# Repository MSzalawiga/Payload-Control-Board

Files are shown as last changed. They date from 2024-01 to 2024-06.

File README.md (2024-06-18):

# Payload Control Board

During the 2023-2024 design cycle I was tasked with updating the Control Board for the Scientific Payload for Queen's Space Engineering Team.

I worked on 2 revisions of the board being Rev2 and Rev3 with Rev3 being the board used at competition.

These boards were created using KiCad 7.0 and were both 4 layer Signal/Ground/Power/Signal stackups.

## Revision 2
Revision 2 was done in a hurry as we needed a working control board for our systems acceptance review in late Feburary 2024, meaning I needed to order the board early December 2023 before exams started. The hurry comes from the fact that I took over this project from scratch in late November 2023.

### Scope and Functional Requirements
The scope and requirements of this control board came from the requirements from the Science and Mechanical team along with the 2024 University Rover Challenge (URC) Science mission rules. The scope and requirements were as follows:
- Control 2 Stepper Motors to raise and lower the payload
- Control up to 6 Servos for collection scoops and an auger
- Be able to toggle and change the brightness of 9 incandescent lights for the on-board spectrometer.
- Interface with the Rover through serial communication
- Interface with Sensors to get scientific measurements
### Reflection
I am content the turnout of this board, although the board was not space efficent it was able to serve its purpose in being able to provide funcionality for the systems acceptance review. 
Also since I was only able to use THT components (annoying I know) I couldn't find a buck converter with an external control pin, thankfully a weird trick I found online (can't find the articel :(  using a dac to influence the reading on the feedback pin worked wonderfully.

## Revision 3
Now having more time I created Revision 3, having mostly the same requirements with some exceptions being no more ethernet module, switch 3 lights for UV lights and the sensors switching it was pretty much the same. Also I could use SMT components (thank god). 

I am going to jump right into the reflection since the requirements were basically the same as revision 2.

### Reflection
Awesome, I am very happy with the turnout of this board. I was able to fit everything on a 100mm x 100mm board with a Teensy 4.1 microcontroller with a footprint of ~ 60mm x 25 mm. Also this was my first time soldering SMT components on a PCB so I chose 0603 (metric) to be my smallest passive size and I think it turned out well.

A new revision will be needed next year to adapt to the changing ruleset of the science mission. Next year I have taken on an executive position so I will be in more of a helper / design verification role for this specific project.

Some improvements I can think of are:
- No teensy 4.1, switch to STM32 they are just better and putting the MCU ourselves results in a smaller footprint and a more professional look
- I accidentally swapped SDA and SCL on the 3V3 I2C line (whoops) but with design verification next year this shouldn't happen
- For controlling light brightness use PWM and Transistors rather than a buck converter, the lights don't draw too much current. or use a newer buck ic with external pwm signal
- get new stepper drivers, current ones ran very hot and weren't very configurable

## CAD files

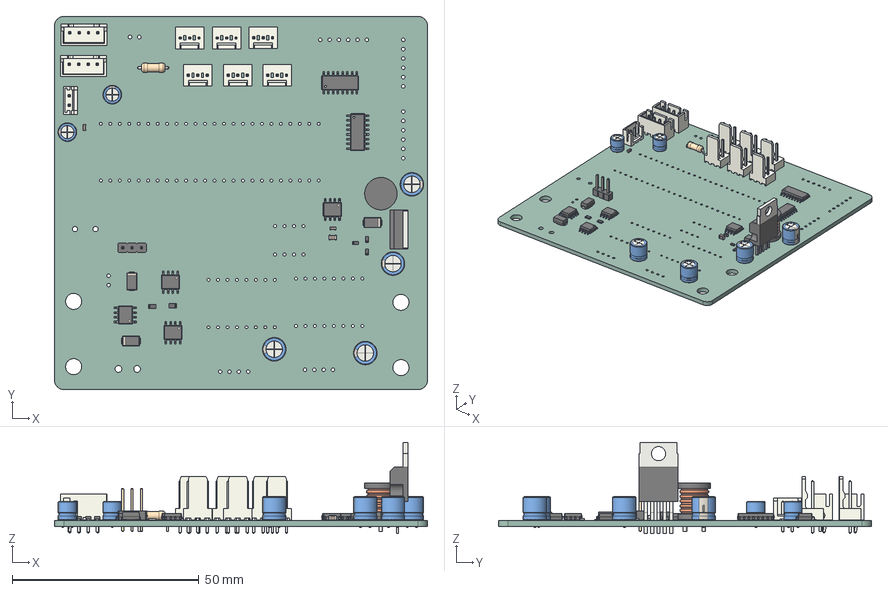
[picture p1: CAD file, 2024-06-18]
Rev3/PayloadPcbRev3.step
100.0 x 100.0 x 24.4 mm
L_Radial_D8.7mm_P5.00mm_Fastron_07HCP
R_0603_1608Metric x 3
SOIC_8_39x49mm_P127mm x 4
Molex_AE_6410_03A x 6
TO_220_5_Pentawatt_Multiwatt_5_Vertical
R_0805_2012Metric x 2
PinHeader_1x03_P254mm_Vertical
CP_Radial_D50mm_P250mm x 2
C_0805_2012Metric
CP_Radial_D63mm_P250mm x 4
C_0603_1608Metric x 2
JST_B4B_XH_A x 2
JST_B2B_EH_A
R_Axial_DIN0207_L63mm_D25mm_P762mm_Horizontal
D_SMA x 3
SOIC_16_39x99mm_P127mm x 2
PayloadPcbRev3_PCB

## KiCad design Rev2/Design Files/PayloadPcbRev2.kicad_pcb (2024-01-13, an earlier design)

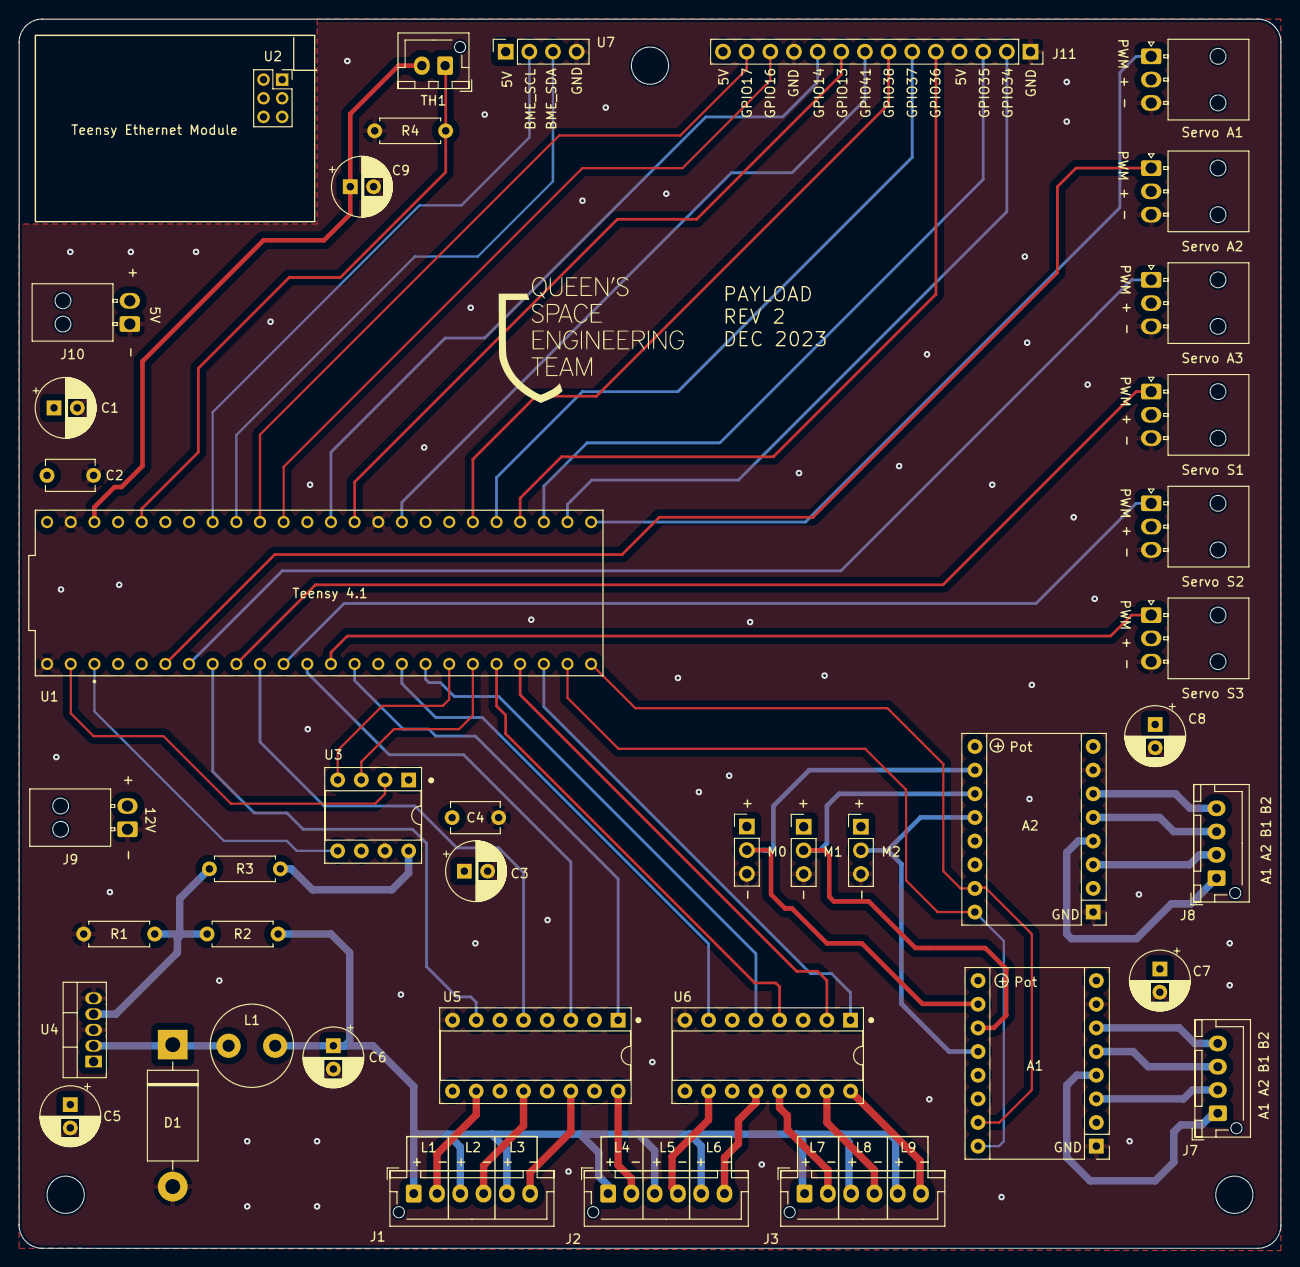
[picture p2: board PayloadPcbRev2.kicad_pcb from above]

Board: 4 copper layers, 135.5 x 132.0 mm, 42 parts (0 on the bottom side), 62 nets.

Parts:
A1, A2: DRV8825_Stepper_Driver; Pololu_Breakout-16_15.2x20.3mm
C1, C3, C9: 47u; CP_Radial_D6.3mm_P2.50mm
C2, C4: 100n; C_Disc_D5.1mm_W3.2mm_P5.00mm
C5, C6, C7, C8: 100u; CP_Radial_D6.3mm_P2.50mm
D1: 1N5821; D_DO-201AD_P15.24mm_Horizontal
J1: Lights Row 1; JST_XH_B6B-XH-AM_1x06_P2.50mm_Vertical
J2: Lights Row 2; JST_XH_B6B-XH-AM_1x06_P2.50mm_Vertical
J3: Lights Row 3; JST_XH_B6B-XH-AM_1x06_P2.50mm_Vertical
J4: M0 Jumper; PinHeader_1x03_P2.54mm_Vertical
J5: M1 Jumper; PinHeader_1x03_P2.54mm_Vertical
J6: M2 Jumper; PinHeader_1x03_P2.54mm_Vertical
J7: Stepper Motor 1; JST_XH_B4B-XH-AM_1x04_P2.50mm_Vertical
J8: Stepper Motor 2; JST_XH_B4B-XH-AM_1x04_P2.50mm_Vertical
J9: 12V Connector; Molex_Nano-Fit_105313-xx02_1x02_P2.50mm_Horizontal
J10: 5V Connector; Molex_Nano-Fit_105313-xx02_1x02_P2.50mm_Horizontal
J11: Extra Connections Header; PinSocket_1x14_P2.54mm_Vertical
L1: 220u; L_Radial_D8.7mm_P5.00mm_Fastron_07HCP
M1: Servo A1; Molex_Nano-Fit_105313-xx03_1x03_P2.50mm_Horizontal
M2: Servo A2; Molex_Nano-Fit_105313-xx03_1x03_P2.50mm_Horizontal
M3: Servo A3; Molex_Nano-Fit_105313-xx03_1x03_P2.50mm_Horizontal
M4: Servo S1; Molex_Nano-Fit_105313-xx03_1x03_P2.50mm_Horizontal
M5: Servo S2; Molex_Nano-Fit_105313-xx03_1x03_P2.50mm_Horizontal
M6: Servo S3; Molex_Nano-Fit_105313-xx03_1x03_P2.50mm_Horizontal
R1: 1k6; R_Axial_DIN0207_L6.3mm_D2.5mm_P7.62mm_Horizontal
R2: 10k; R_Axial_DIN0207_L6.3mm_D2.5mm_P7.62mm_Horizontal
R3: 5k1; R_Axial_DIN0207_L6.3mm_D2.5mm_P7.62mm_Horizontal
R4: 100k; R_Axial_DIN0207_L6.3mm_D2.5mm_P7.62mm_Horizontal
TH1: Thermistor; JST_XH_B2B-XH-AM_1x02_P2.50mm_Vertical
U1: Teensy 4.1; Teensy4-1
U2: Teensy ETH Module Connnector; PinSocket_2x03_P2.00mm_Vertical
U3: MCP4921-EP; DIP-8_W7.62mm_Socket
U4: LM2576T-ADJG; TO-220-5_Vertical
U5, U6: ULN2003A; DIP-16_W7.62mm_Socket
U7: BME 680 Module; PinSocket_1x04_P2.54mm_Vertical

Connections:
+5V: A1.13 (~RST), A1.14 (~SLP), A2.13 (~RST), A2.14 (~SLP), C1.1, C2.1, C3.1, C4.1, J4.1, J5.1, J6.1, J10.2, J11.4, J11.14, M1.2 (+), M2.2 (+), M3.2 (+), M4.2 (+), M5.2 (+), M6.2 (+), U1.VIN, U3.1 (VDD), U3.6 (VrefA), U7.1 (Vin)
+12V: A1.8 (VMOT), A2.8 (VMOT), C5.1, C7.1, C8.1, J9.2, U4.1 (VIN)
/Lights Control/DAC_CS: U1.0 (GPIO0), U3.2 (~CS)
/Lights Control/DAC_MOSI: U1.26 (A12/GPIO26), U3.4 (SDI)
/Lights Control/DAC_SCK: U1.27 (A13/GPIO27), U3.3 (SCK)
/Lights Control/FB: R1.1, R2.2, R3.1, U4.4 (FB)
/Lights Control/L1: U1.6 (GPIO6), U5.7 (I7)
/Lights Control/L2: U1.8 (GPIO8), U5.5 (I5)
/Lights Control/L3: U1.10 (GPIO10), U5.3 (I3)
/Lights Control/L4: U1.12 (GPIO12), U5.1 (I1)
/Lights Control/L5: U1.24 (A10/GPIO24), U6.7 (I7)
/Lights Control/L6: U1.25 (A11/GPIO25), U6.5 (I5)
/Lights Control/L7: U1.28 (GPIO28), U6.4 (I4)
/Lights Control/L8: U1.29 (GPIO29), U6.2 (I2)
/Lights Control/L9: U1.30 (GPIO30), U6.1 (I1)
/Lights Control/LDAC: U1.1 (GPIO1), U3.5 (~LDAC)
/Lights Control/LM2576_Out: D1.1 (K), L1.1, U4.2 (OUT)
/Motors/Dir: A1.16 (DIR), A2.16 (DIR), U1.31 (GPIO31)
/Motors/Servo A1 PWM: M1.1 (PWM), U1.33 (GPIO33)
/Motors/Servo A2 PWM: M2.1 (PWM), U1.4 (GPIO4)
/Motors/Servo A3 PWM: M3.1 (PWM), U1.5 (GPIO5)
/Motors/Servo S1 PWM: M4.1 (PWM), U1.7 (GPIO7)
/Motors/Servo S2 PWM: M5.1 (PWM), U1.9 (GPIO9)
/Motors/Servo S3 PWM: M6.1 (PWM), U1.11 (GPIO11)
/Motors/Step: A1.15 (STEP), A2.15 (STEP), U1.32 (GPIO32)
/Sensors and Connectors/3V3: C9.1, TH1.2, U1.3.3V_2 (3.3V__1)
/Sensors and Connectors/BME_SCL: U1.19 (A5/GPIO19), U7.4 (SCK/SCL)
/Sensors and Connectors/BME_SDA: U1.18 (A4/GPIO18), U7.6 (SDI/SDA)
/Sensors and Connectors/GPIO13: J11.9, U1.13 (GPIO13)
/Sensors and Connectors/GPIO14: J11.10, U1.14 (A0/GPIO14)
/Sensors and Connectors/GPIO16: J11.12, U1.16 (A2/GPIO16)
/Sensors and Connectors/GPIO17: J11.13, U1.17 (A3/GPIO17)
/Sensors and Connectors/GPIO34: J11.2, U1.34 (GPIO34)
/Sensors and Connectors/GPIO35: J11.3, U1.35 (GPIO35)
/Sensors and Connectors/GPIO36: J11.5, U1.36 (GPIO36)
/Sensors and Connectors/GPIO37: J11.6, U1.37 (GPIO37)
/Sensors and Connectors/GPIO38: J11.7, U1.38 (A14/GPIO38)
/Sensors and Connectors/GPIO41: J11.8, U1.41 (A17/GPIO41)
/Sensors and Connectors/V_Thermo: R4.1, TH1.1, U1.22 (A8/GPIO22)
GND: A1.1 (GND), A1.7 (GND_MOT), A2.1 (GND), A2.7 (GND_MOT), C1.2, C2.2, C3.2, C4.2, C5.2, C6.2, C7.2, C8.2, C9.2, D1.2 (A), J4.3, J5.3, J6.3, J9.1, J10.1, J11.1, J11.11, M1.3 (-), M2.3 (-), M3.3 (-), M4.3 (-), M5.3 (-), M6.3 (-), R1.2, R4.2, U1.GND1 (GND), U1.GND2 (GND), U1.GND3 (GND), U3.7 (AVSS), U4.3 (GND), U4.5 (~ON/OFF), U5.8 (GND), U6.8 (GND), U7.3 (GND)
L1_GND: J1.2, U5.10 (O7)
L2_GND: J1.4, U5.12 (O5)
L3_GND: J1.6, U5.14 (O3)
L4_GND: J2.2, U5.16 (O1)
L5_GND: J2.4, U6.10 (O7)
L6_GND: J2.6, U6.12 (O5)
L7_GND: J3.2, U6.13 (O4)
L8_GND: J3.4, U6.15 (O2)
L9_GND: J3.6, U6.16 (O1)
Light_PWR: C6.1, J1.1, J1.3, J1.5, J2.1, J2.3, J2.5, J3.1, J3.3, J3.5, L1.2, R2.1
M0: A1.10 (M0), A2.10 (M0), J4.2
M1: A1.11 (M1), A2.11 (M1), J5.2
M2: A1.12 (M2), A2.12 (M2), J6.2
Step1_A1: A1.4 (A1), J7.1
Step1_A2: A1.3 (A2), J7.2
Step1_B1: A1.5 (B1), J7.3
Step1_B2: A1.6 (B2), J7.4
Step2_A1: A2.4 (A1), J8.1
Step2_A2: A2.3 (A2), J8.2
Step2_B1: A2.5 (B1), J8.3
Step2_B2: A2.6 (B2), J8.4
Vctrl: R3.2, U3.8 (VoutA)

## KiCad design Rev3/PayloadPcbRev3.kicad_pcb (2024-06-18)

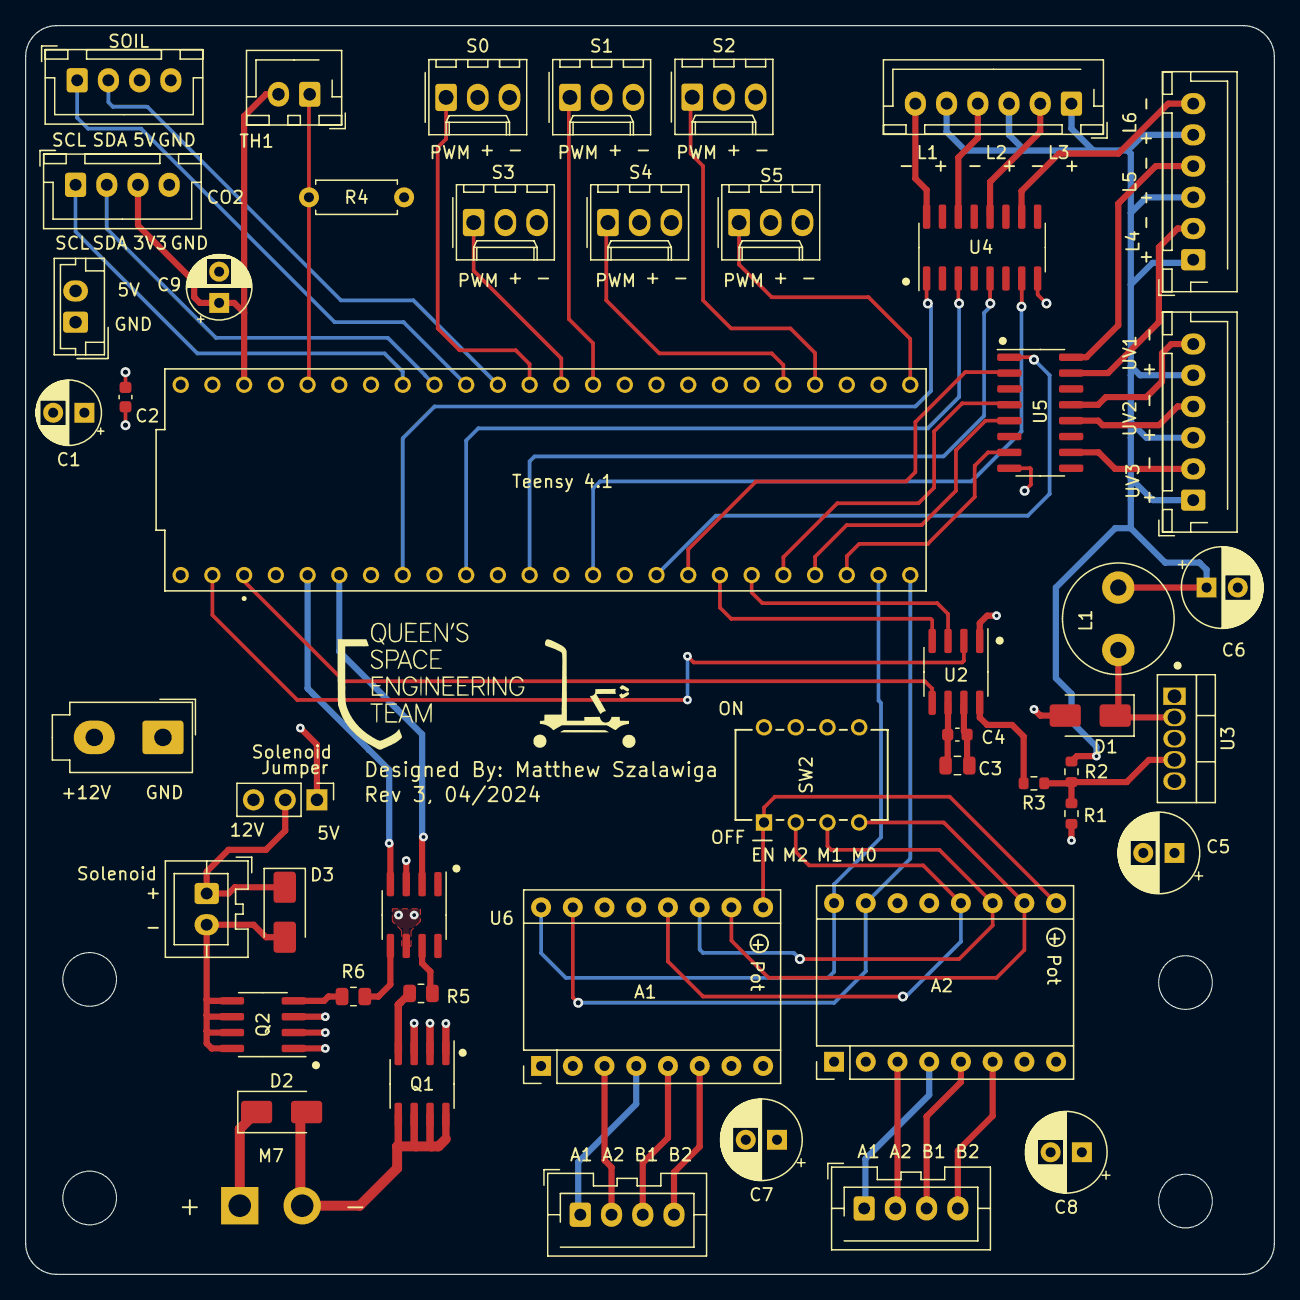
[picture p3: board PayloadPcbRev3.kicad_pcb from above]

Board: 4 copper layers, 100.0 x 100.0 mm, 53 parts (0 on the bottom side), 64 nets.

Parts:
A1, A2: DRV8825_Stepper_Driver; Pololu_Breakout-16_15.2x20.3mm
C1, C9: 47u; CP_Radial_D5.0mm_P2.50mm
C2, C4: 100n; C_0603_1608Metric
C3: 10u; C_0805_2012Metric
C5, C6, C7, C8: 100u; CP_Radial_D6.3mm_P2.50mm
CO2: CO2 Sensor (STC31); JST_XH_B4B-XH-A_1x04_P2.50mm_Vertical
D1, D2, D3: SS54; D_SMA
H1, H2, H3, H4: MountingHole; MountingHole_4.3mm_M4
J1: Lights Row 1; JST_XH_B6B-XH-AM_1x06_P2.50mm_Vertical
J2: Lights Row 2; JST_XH_B6B-XH-AM_1x06_P2.50mm_Vertical
J3: Lights Row 3; JST_XH_B6B-XH-AM_1x06_P2.50mm_Vertical
J6: 5V Solenoid; JST_XA_B02B-XASK-1_1x02_P2.50mm_Vertical
J7: Stepper Motor 1; JST_XA_B04B-XASK-1-A_1x04_P2.50mm_Vertical
J8: Stepper Motor 2; JST_XA_B04B-XASK-1-A_1x04_P2.50mm_Vertical
J9: 12V Connector; Molex_Mini-Fit_Jr_5566-02A_2x01_P4.20mm_Vertical
J10: 5V Connector; JST_EH_B2B-EH-A_1x02_P2.50mm_Vertical
J12: Solenoid jumper; PinHeader_1x03_P2.54mm_Vertical
L1: 220u; L_Radial_D8.7mm_P5.00mm_Fastron_07HCP
M7: Motor_DC; AMASS_XT30UPB-F_1x02_P5.0mm_Vertical
Q1, Q2: AO4484; SOIC-8_3.9x4.9mm_P1.27mm
R1: 1k6; R_0603_1608Metric
R2: 10k; R_0603_1608Metric
R3: 5k1; R_0603_1608Metric
R4: 100k; R_Axial_DIN0207_L6.3mm_D2.5mm_P7.62mm_Horizontal
R5, R6: 0R; R_0805_2012Metric
S0: Servo S0; Molex_KK-254_AE-6410-03A_1x03_P2.54mm_Vertical
S1: Servo S1; Molex_KK-254_AE-6410-03A_1x03_P2.54mm_Vertical
S2: Servo S2; Molex_KK-254_AE-6410-03A_1x03_P2.54mm_Vertical
S3: Servo S3; Molex_KK-254_AE-6410-03A_1x03_P2.54mm_Vertical
S4: Servo S4; Molex_KK-254_AE-6410-03A_1x03_P2.54mm_Vertical
S5: Servo S5; Molex_KK-254_AE-6410-03A_1x03_P2.54mm_Vertical
SOIL: Adafruit STEMMA Soil Sensor; JST_XH_B4B-XH-A_1x04_P2.50mm_Vertical
SW2: SW_DIP_x04; DIP8_210-4_CTS
TH1: Thermistor; JST_XH_B2B-XH-AM_1x02_P2.50mm_Vertical
Teensy 4.1: Teensy 4.1; Teensy4-1
U2: MCP4921-ESN; SOIC-8_3.9x4.9mm_P1.27mm
U3: LM2576T-ADJ; TO-220-5_Vertical
U4, U5: ULN2003A; SOIC-16_3.9x9.9mm_P1.27mm
U6: MIC4427; SOIC-8_3.9x4.9mm_P1.27mm

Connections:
+5V: A1.13 (~RST), A1.14 (~SLP), A2.13 (~RST), A2.14 (~SLP), C1.1, C2.1, C3.1, C4.1, J10.2, J12.1, S0.2 (+), S1.2 (+), S2.2 (+), S3.2 (+), S4.2 (+), S5.2 (+), SOIL.3, SW2.5, SW2.6, SW2.7, SW2.8, Teensy 4.1.VIN, U2.1 (VDD), U2.6 (VrefA)
+12V: A1.8 (VMOT), A2.8 (VMOT), C5.1, C7.1, C8.1, D2.1 (K), J9.2, J12.3, M7.1 (+), U3.1 (VIN), U6.6 (V+)
/Lights Control/DAC_CS: Teensy 4.1.0 (GPIO0), U2.2 (~CS)
/Lights Control/DAC_MOSI: Teensy 4.1.26 (A12/GPIO26), U2.4 (SDI)
/Lights Control/DAC_SCK: Teensy 4.1.27 (A13/GPIO27), U2.3 (SCK)
/Lights Control/FB: R1.1, R2.2, R3.1, U3.4 (FB)
/Lights Control/L1: Teensy 4.1.6 (GPIO6), U4.1 (I1)
/Lights Control/L2: Teensy 4.1.8 (GPIO8), U4.3 (I3)
/Lights Control/L3: Teensy 4.1.10 (GPIO10), U4.5 (I5)
/Lights Control/L4: Teensy 4.1.12 (GPIO12), U4.7 (I7)
/Lights Control/L5: Teensy 4.1.24 (A10/GPIO24), U5.1 (I1)
/Lights Control/L6: Teensy 4.1.25 (A11/GPIO25), U5.2 (I2)
/Lights Control/LDAC: Teensy 4.1.1 (GPIO1), U2.5 (~LDAC)
/Lights Control/LM2576_Out: D1.1 (K), L1.1, U3.2 (OUT)
/Lights Control/UV1: Teensy 4.1.28 (GPIO28), U5.4 (I4)
/Lights Control/UV2: Teensy 4.1.29 (GPIO29), U5.5 (I5)
/Lights Control/UV3: Teensy 4.1.30 (GPIO30), U5.7 (I7)
/Motors/Dir: A1.16 (DIR), A2.16 (DIR), Teensy 4.1.31 (GPIO31)
/Motors/M-: D2.2 (A), M7.2 (-), Q1.5 (D), Q1.6 (D), Q1.7 (D), Q1.8 (D)
/Motors/OutA_to_R: R5.1, U6.7 (OUT_A)
/Motors/OutB_to_R: R6.1, U6.5 (OUT_B)
/Motors/Servo S0 PWM: S0.1 (PWM), Teensy 4.1.15 (A1/GPIO15)
/Motors/Servo S1 PWM: S1.1 (PWM), Teensy 4.1.13 (GPIO13)
/Motors/Servo S2 PWM: S2.1 (PWM), Teensy 4.1.36 (GPIO36)
/Motors/Servo S3 PWM: S3.1 (PWM), Teensy 4.1.14 (A0/GPIO14)
/Motors/Servo S4 PWM: S4.1 (PWM), Teensy 4.1.37 (GPIO37)
/Motors/Servo S5 PWM: S5.1 (PWM), Teensy 4.1.33 (GPIO33)
/Motors/Solenoid_+: D3.1 (K), J6.1, J12.2
/Motors/Solenoid_-: D3.2 (A), J6.2, Q2.5 (D), Q2.6 (D), Q2.7 (D), Q2.8 (D)
/Motors/Step: A1.15 (STEP), A2.15 (STEP), Teensy 4.1.32 (GPIO32)
/Motors/motor_pwm: Teensy 4.1.4 (GPIO4), U6.2 (IN_A)
/Motors/solenoid_pwm: Teensy 4.1.3 (GPIO3), U6.4 (IN_B)
/Sensors and Connectors/3V3: C9.1, CO2.3, TH1.2, Teensy 4.1.3.3V_2 (3.3V__1)
/Sensors and Connectors/I2C_SCL0: CO2.1, Teensy 4.1.19 (A5/GPIO19)
/Sensors and Connectors/I2C_SCL1: SOIL.1, Teensy 4.1.17 (A3/GPIO17)
/Sensors and Connectors/I2C_SDA0: CO2.2, Teensy 4.1.18 (A4/GPIO18)
/Sensors and Connectors/I2C_SDA1: SOIL.2, Teensy 4.1.16 (A2/GPIO16)
/Sensors and Connectors/V_Thermo: R4.1, TH1.1, Teensy 4.1.22 (A8/GPIO22)
EN_N: A1.9 (~EN), A2.9 (~EN), SW2.1
GND: A1.1 (GND), A1.7 (GND_MOT), A2.1 (GND), A2.7 (GND_MOT), C1.2, C2.2, C3.2, C4.2, C5.2, C6.2, C7.2, C8.2, C9.2, CO2.4, D1.2 (A), J9.1, J10.1, Q1.1 (S), Q1.2 (S), Q1.3 (S), Q2.1 (S), Q2.2 (S), Q2.3 (S), R1.2, R4.2, S0.3 (-), S1.3 (-), S2.3 (-), S3.3 (-), S4.3 (-), S5.3 (-), SOIL.4, Teensy 4.1.GND1 (GND), Teensy 4.1.GND2 (GND), Teensy 4.1.GND3 (GND), U2.7 (AVSS), U3.3 (GND), U3.5 (~ON/OFF), U4.8 (GND), U5.8 (GND), U6.3 (GND)
L1_GND: J1.6, U4.16 (O1)
L2_GND: J1.4, U4.14 (O3)
L3_GND: J1.2, U4.12 (O5)
L4_GND: J2.6, U4.10 (O7)
L5_GND: J2.4, U5.16 (O1)
L6_GND: J2.2, U5.15 (O2)
Light_PWR: C6.1, J1.1, J1.3, J1.5, J2.1, J2.3, J2.5, J3.1, J3.3, J3.5, L1.2, R2.1
M0: A1.10 (M0), A2.10 (M0), SW2.4
M1: A1.11 (M1), A2.11 (M1), SW2.3
M2: A1.12 (M2), A2.12 (M2), SW2.2
Step1_A1: A1.4 (A1), J7.1
Step1_A2: A1.3 (A2), J7.2
Step1_B1: A1.5 (B1), J7.3
Step1_B2: A1.6 (B2), J7.4
Step2_A1: A2.4 (A1), J8.1
Step2_A2: A2.3 (A2), J8.2
Step2_B1: A2.5 (B1), J8.3
Step2_B2: A2.6 (B2), J8.4
UV1_GND: J3.6, U5.13 (O4)
UV2_GND: J3.4, U5.12 (O5)
UV3_GND: J3.2, U5.10 (O7)
Vctrl: R3.2, U2.8 (VoutA)
motor_fet: Q1.4 (G), R5.2
solenoid_fet: Q2.4 (G), R6.2

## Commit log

2024-01-13 Uploaded Design Files
    [Connections.kicad_sch, Lights.kicad_sch, MCU_Teensy.kicad_sch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]
2024-06-18 added Rev3
    [Connections.kicad_sch, Lights.kicad_sch, MCU_Teensy.kicad_sch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]
